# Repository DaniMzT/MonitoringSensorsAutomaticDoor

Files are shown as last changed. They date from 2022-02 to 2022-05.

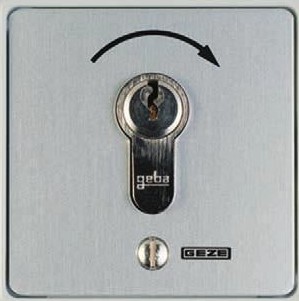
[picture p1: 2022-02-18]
Code/Website_code/htdocs/IoT/images/kb.jpg

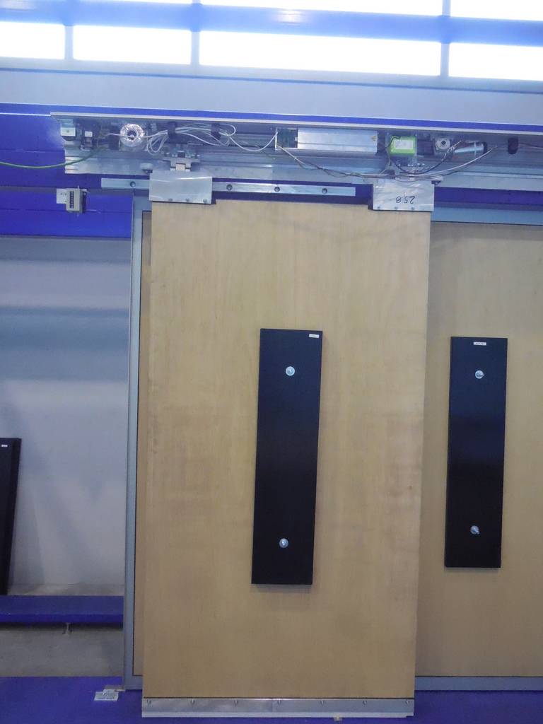
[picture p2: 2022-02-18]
Code/Website_code/htdocs/IoT/images/wooden_door-vertical.jpg

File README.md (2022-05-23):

# MonitoringSensorsAutomaticDoor
This project is a university thesis carried out in the company GEZE, focused on the automatic sliding doors tested in the laboratory. 
However, it can be extended to generic monitoring projects.
The targets of the project are:
- To acquire data from external sensors (current, temperature, humidity, position, speed and cycles)
- To save the data into a database
- To display live data and maximum/minimum values on a website, as well as providing other functionalities for the test engineers like:
  - Notification of alarms (based on the limits set by the engineers on the website) on the website and by email (email accounts registered on the website)
  - Download some specific data of tests from a specified date range 
  - Watch live streaming of the test benches (FOSCAM IP camera)
  - Perform remote activations on the bench (open/stop)

A NodeMCU is the main controller, acquiring the sensors data and sending the processed data via WiFi to a database (with a PHP file as a bridge).
There is an Arduino UNO for the acquisition of position, speed (both acquired with a home-made encoder: 2 micro photosensors,emitting to and receiving from a zebra band on the door) and limit switch activations (for door cycles).
The communication between NodeMCU and Arduino UNO is via SoftwareSerial --> not very reliable, it is the main issue to be fixed.
Database and website: based on Bitnami WAMP (package for Windows, Apache, MySQL and PHP)

Files in the project:
- Code: website, micros (NodeMCU and Arduino UNO) and database (MySQL)
- KiCAD files (to be added): schematic and printed boards

ISSUES TO BE FIXED:
- Communication between NodeMCU and Arduino UNO. SoftwareSerial is not reliable, I am afraid it is not due to my code. 
I will try to switch ports so that I can use SPI communication (currently, the SPI ports are used as GPIOs)
- Website security is weak. I have been self-learning web programming on the fly --> User identifications, work with JavaScript to process the forms, etc.

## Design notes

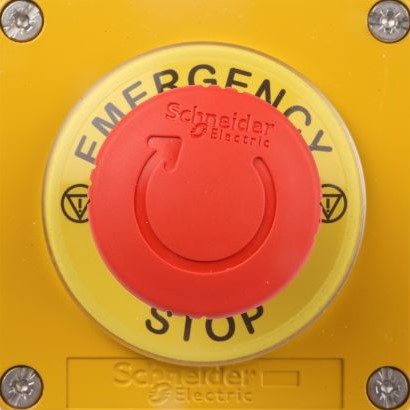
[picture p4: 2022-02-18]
Code/Website_code/htdocs/IoT/images/emStop.jpg

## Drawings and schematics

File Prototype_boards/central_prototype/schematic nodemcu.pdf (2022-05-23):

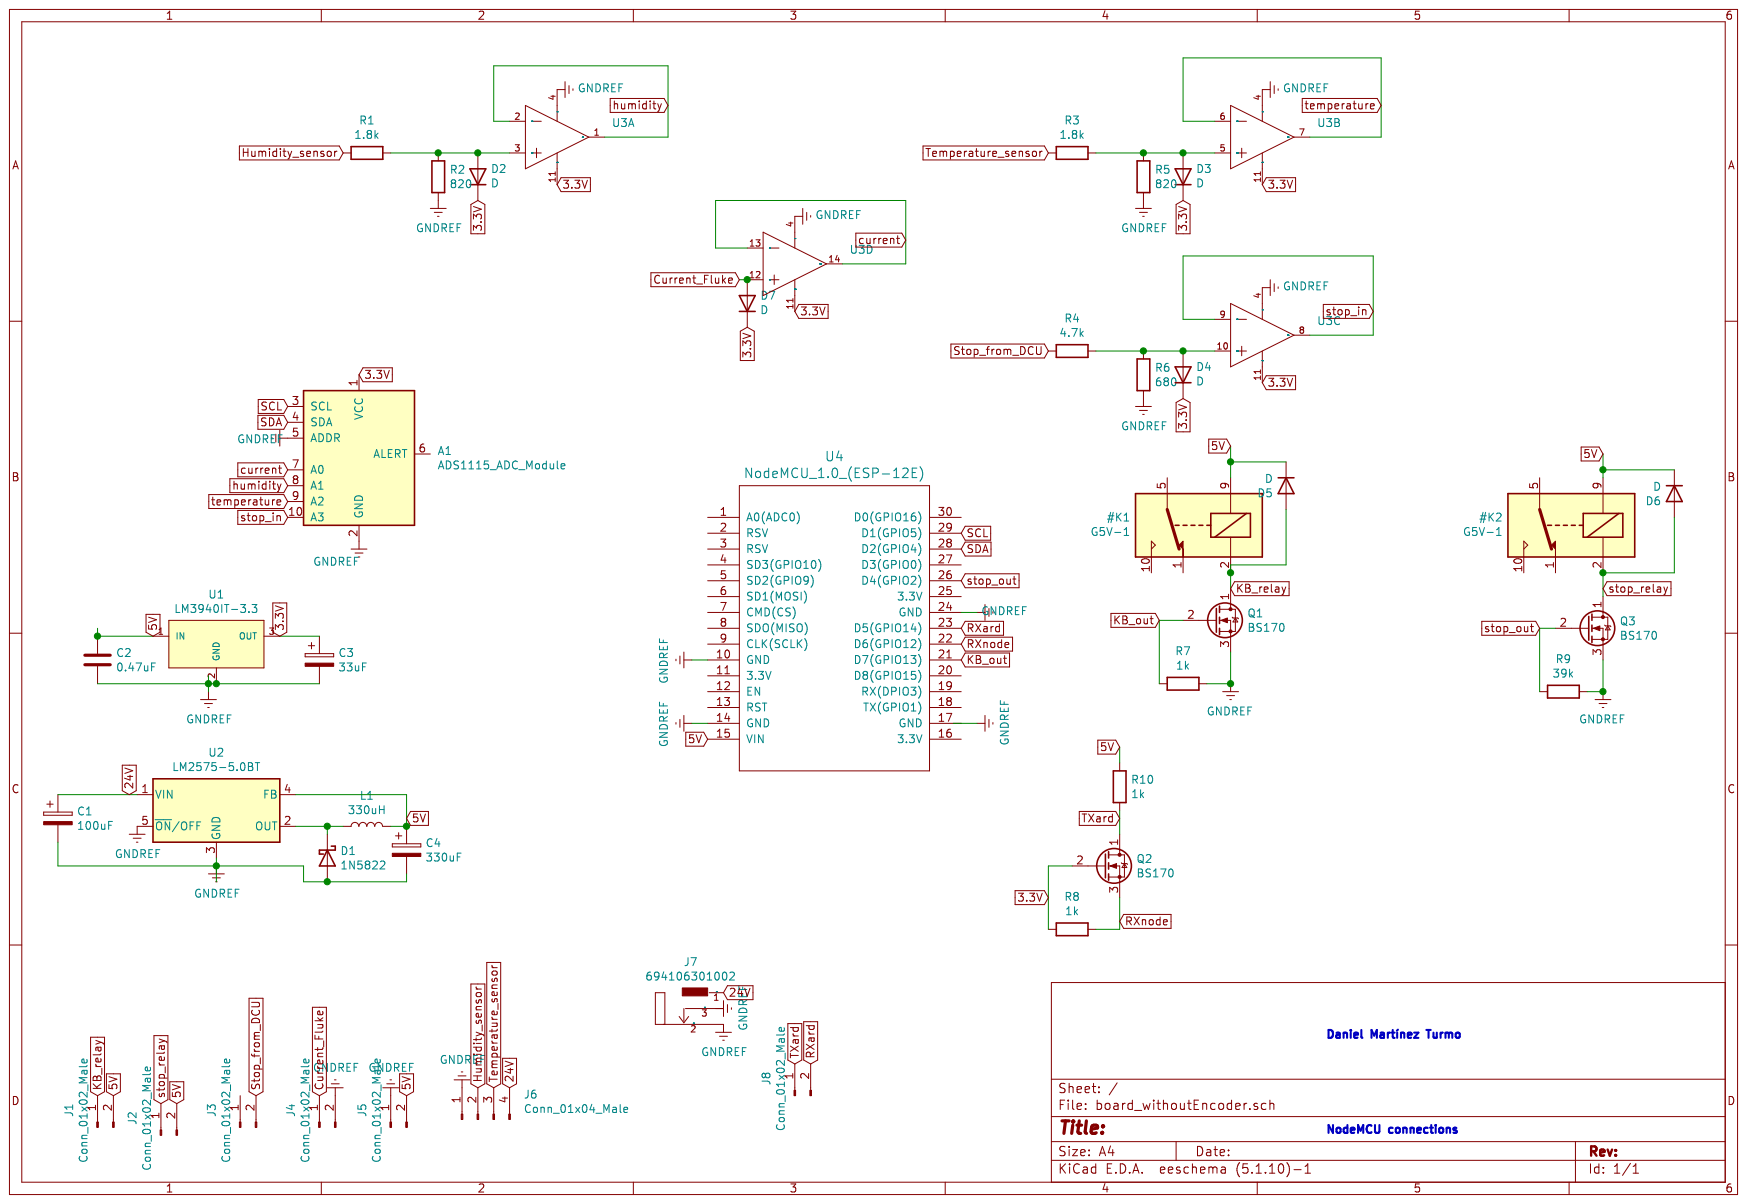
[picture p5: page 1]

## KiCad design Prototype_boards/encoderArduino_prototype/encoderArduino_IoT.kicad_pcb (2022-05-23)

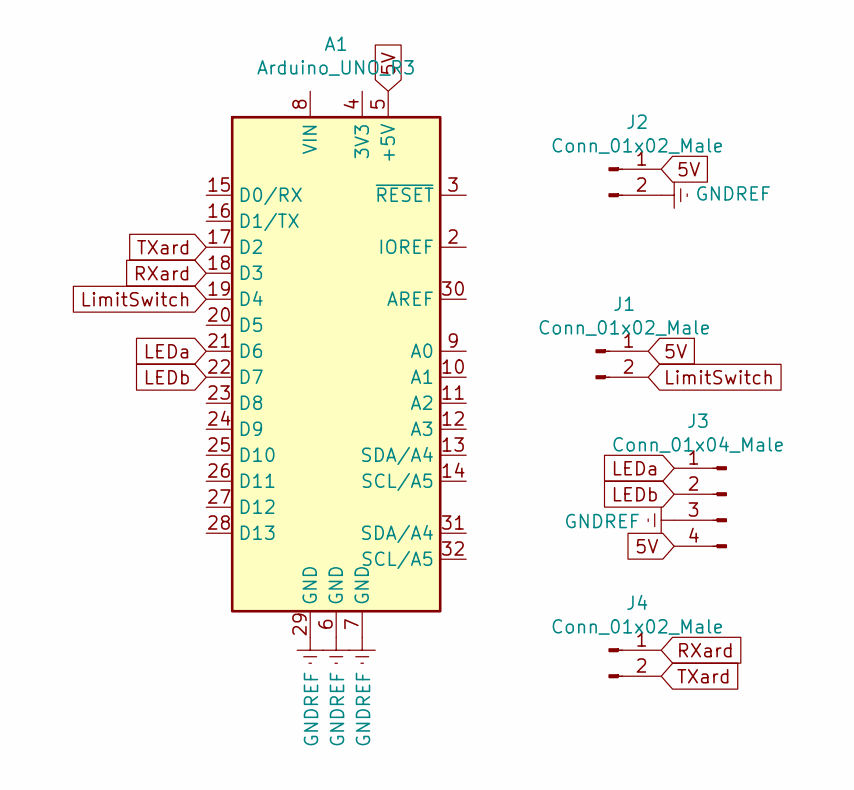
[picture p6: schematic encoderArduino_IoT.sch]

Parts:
A1: Arduino_UNO_R3; Arduino_UNO_R3_WithMountingHoles
J1, J2, J4: Conn_01x02_Male; PhoenixContact_MC_1,5_2-G-3.5_1x02_P3.50mm_Horizontal
J3: Conn_01x04_Male; PhoenixContact_MC_1,5_4-G-3.5_1x04_P3.50mm_Horizontal

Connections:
5V: A1.5 (+5V), J1.1, J2.1, J3.4
GNDREF: A1.6 (GND), A1.7 (GND), A1.29 (GND), J2.2, J3.3
LEDa: A1.21 (D6), J3.1
LEDb: A1.22 (D7), J3.2
LimitSwitch: A1.19 (D4), J1.2
RXard: A1.18 (D3), J4.1
TXard: A1.17 (D2), J4.2

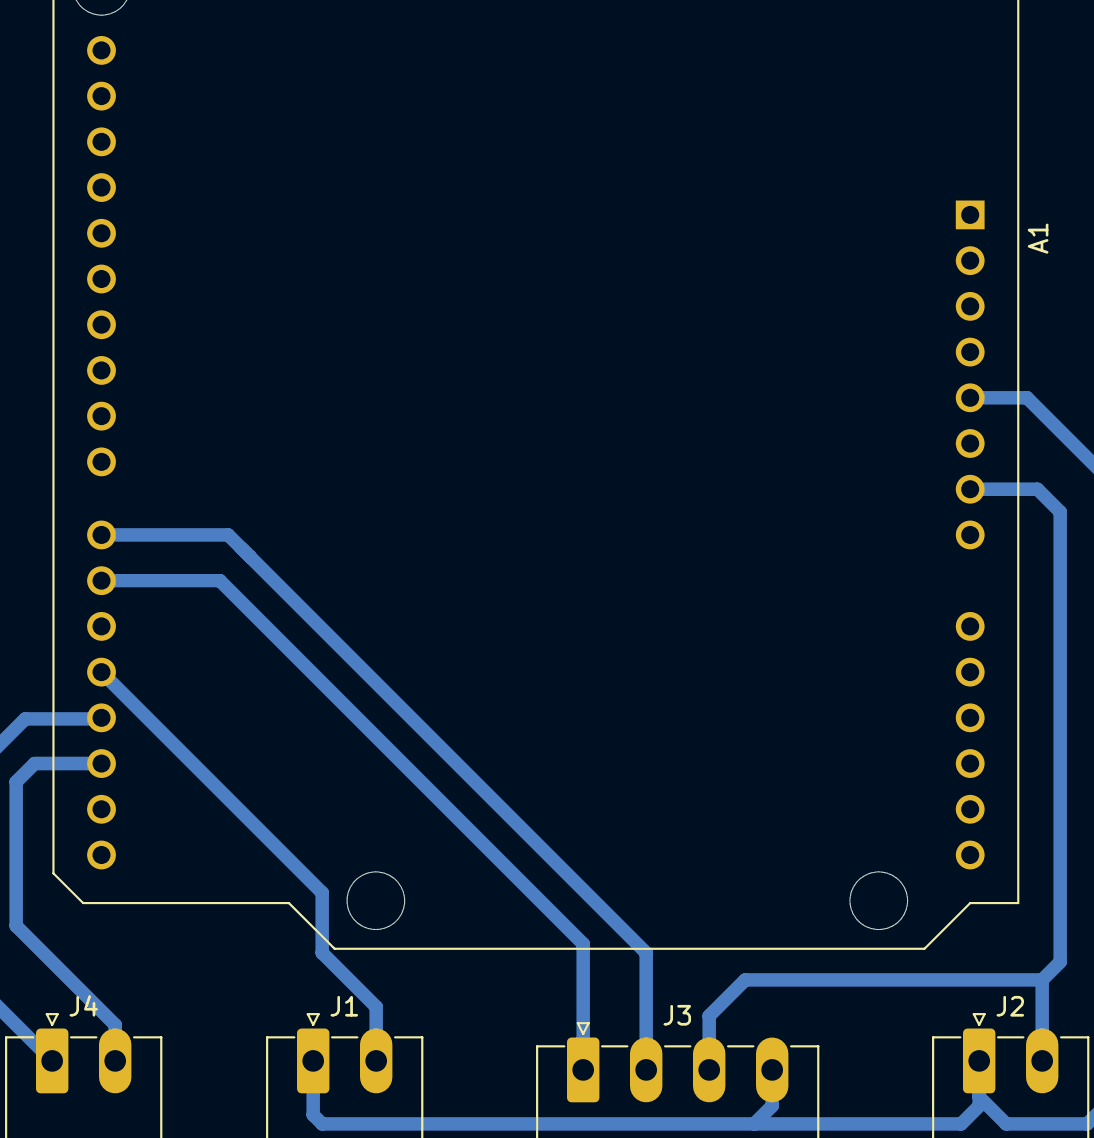
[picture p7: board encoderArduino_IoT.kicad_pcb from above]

Board: 2 copper layers, 5 parts (0 on the bottom side), 7 nets.

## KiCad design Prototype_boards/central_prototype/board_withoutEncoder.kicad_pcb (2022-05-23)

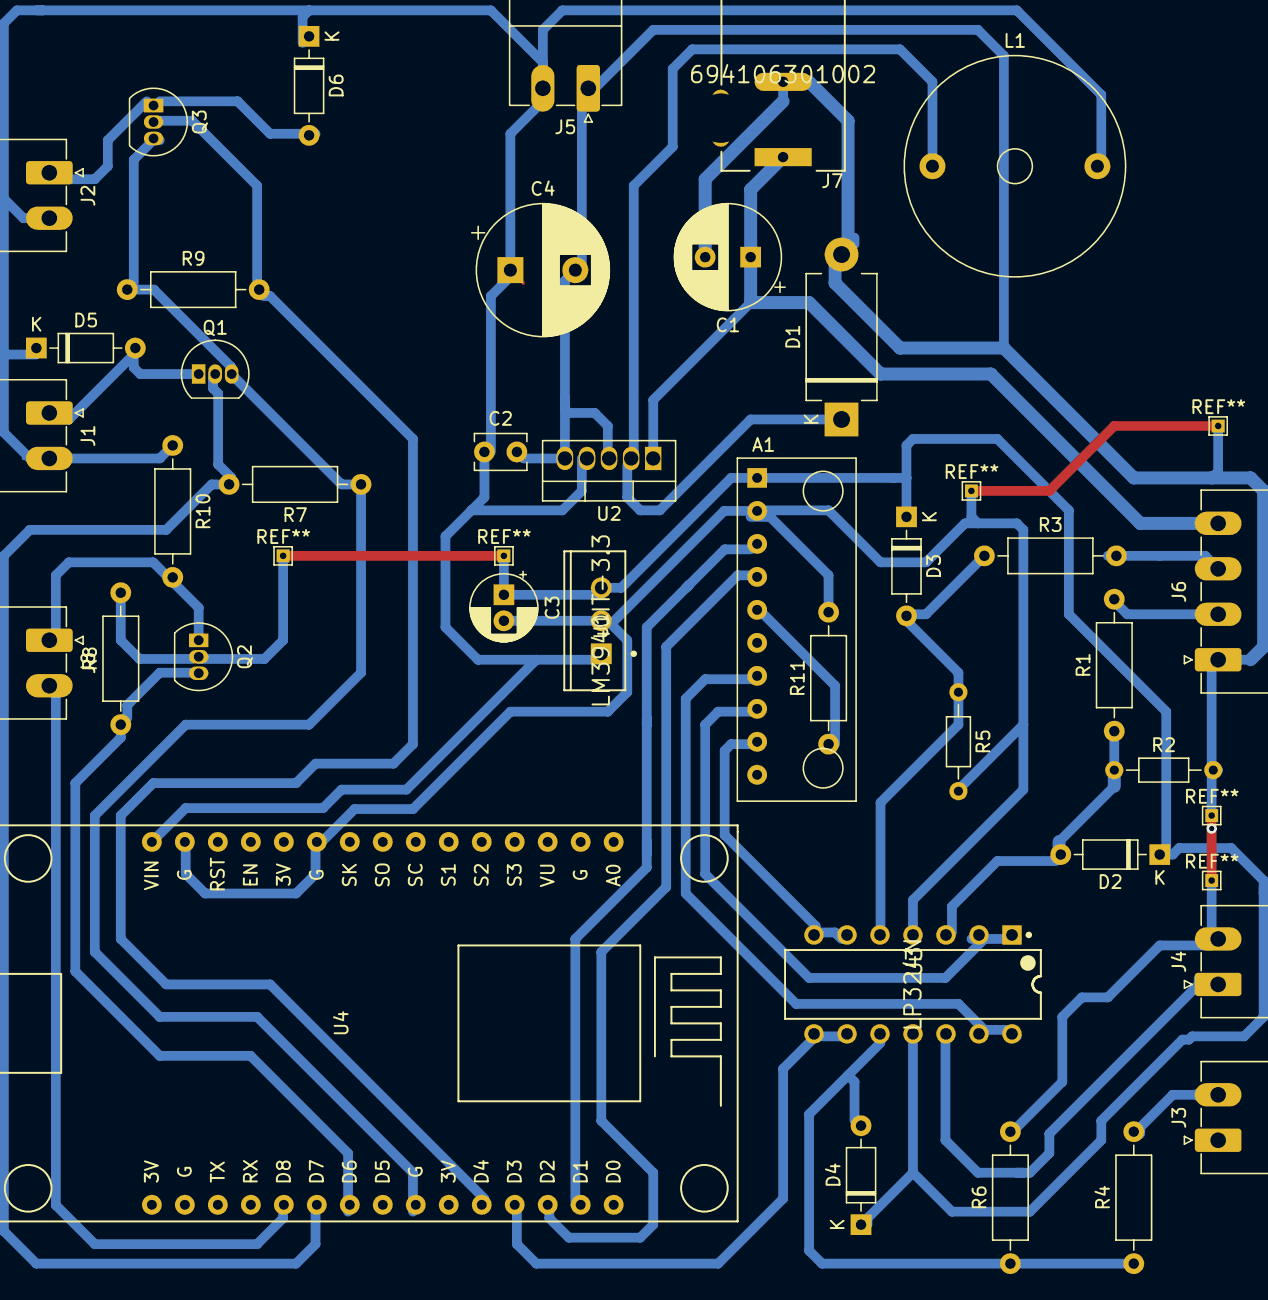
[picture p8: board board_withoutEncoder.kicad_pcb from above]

Board: 2 copper layers, 38 parts (0 on the bottom side), 26 nets.

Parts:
A1: ADS1115_ADC_Module; ADC1115_ADC_Module
C1: 100uF; CP_Radial_D8.0mm_P3.50mm
C2: 0.47uF; C_Disc_D3.8mm_W2.6mm_P2.50mm
C3: 33uF; CP_Radial_D5.0mm_P2.00mm
C4: 330uF; CP_Radial_D10.0mm_P5.00mm
D1: 1N5822; D_DO-201_P12.70mm_Horizontal
D2, D3, D4, D5, D6: D; D_DO-35_SOD27_P7.62mm_Horizontal
J1, J2, J3, J4, J5, J8: Conn_01x02_Male; PhoenixContact_MC_1,5_2-G-3.5_1x02_P3.50mm_Horizontal
J6: Conn_01x04_Male; PhoenixContact_MC_1,5_4-G-3.5_1x04_P3.50mm_Horizontal
J7: 694106301002; Wurth-694106301002-0-0-0
L1: 330uH; L_Radial_D16.8mm_P12.70mm_Vishay_IHB-1
Q1, Q2, Q3: BS170; TO-92_Inline
R1, R3: 1.8k; R_Axial_DIN0207_L6.3mm_D2.5mm_P10.16mm_Horizontal
R2, R5: 820; R_Axial_DIN0204_L3.6mm_D1.6mm_P7.62mm_Horizontal
R4: 4.7k; R_Axial_DIN0207_L6.3mm_D2.5mm_P10.16mm_Horizontal
R6: 680; R_Axial_DIN0207_L6.3mm_D2.5mm_P10.16mm_Horizontal
R7, R8, R9, R10, R11: 1k; R_Axial_DIN0207_L6.3mm_D2.5mm_P10.16mm_Horizontal
U1: LM3940IT-3.3; TI_National_Semiconductor-LM3940IT-3.3-Manufacturer_Recomme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
U2: LM2575-5.0BT; TO-220-5_Vertical
U3: LP324N; Texas_Instruments-LP324N-Manufacturer_Recommended
U4: NodeMCU_1.0_(ESP-12E); NodeMCU1.0(12-E)

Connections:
3.3V: A1.1, C3.1, D2.1, D3.1, D4.1, Q2.2, R8.2, U1.3, U3.11
5V: C2.1, C4.1, D5.1, D6.1, J1.2, J2.2, J5.2, L1.2, R10.1, U1.1, U2.4, U4.15
24V: C1.1, J6.4, J7.1, U2.1
Current_Fluke: J4.1, U3.12
GNDREF: A1.2, C1.2, C2.2, C3.2, C4.2, D1.2, J4.2, J5.1, J6.1, J7.2, Q1.3, Q3.3, R2.2, R5.2, R6.2, R7.1, R9.1, R11.2, U1.2, U2.3, U2.5, U3.4, U4.10, U4.14, U4.17, U4.24
Humidity_sensor: J6.2, R1.2
KB_out: Q1.2, R7.2, U4.21
KB_relay: D5.2, J1.1, Q1.1
unnamed: A1.5, R11.1
unnamed: D1.1, L1.1, U2.2
unnamed: D2.2, R1.1, R2.1, U3.3
unnamed: D3.2, R3.1, R5.1, U3.5
unnamed: D4.2, R4.1, R6.1, U3.10
RXard: J8.2, U4.20
RXnode: Q2.3, R8.1, U4.22
SCL: A1.3, U4.29
SDA: A1.4, U4.28
Stop_from_DCU: J3.2, R4.2
TXard: J8.1, Q2.1, R10.2
Temperature_sensor: J6.3, R3.2
current: A1.7, U3.13, U3.14
humidity: A1.8, U3.1, U3.2
stop_in: U3.8, U3.9, U4.27
stop_out: Q3.2, R9.2, U4.26
stop_relay: D6.2, J2.1, Q3.1
temperature: A1.9, U3.6, U3.7

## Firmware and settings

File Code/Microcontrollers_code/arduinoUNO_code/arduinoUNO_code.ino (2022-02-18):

#include <SoftwareSerial.h> //for software serial communication Arduino-NodeMCU
#include <StreamUtils.h>

const int pinCOUNTER = 4 ; //pin D4 GPIO4 limit switch used as a cycles counter
const int pinLEDA = 6; //pin D6 GPIO6 for LED A used for the encoder
const int pinLEDB = 7; //pin D7 GPIO7 for LED B used for the encoder

bool addCycle = true; //true if new cycle. the number of cycles is stored in database. bool size=1 byte; int size = 2 bytes (if I wanted to use 1 or 0 instead of true or false)
int lastCounter = LOW; //last state of the limit switch. HIGH/LOW from digitalRead is type int
int currentCounter = LOW; //current state of the limit switch
unsigned long time_cycle_begin = millis(); //time when cycle starts. millis() is type unsigned long
unsigned long time_cycle_previous = millis(); //time reading in the previous iteration
unsigned long time_cycle_current = millis(); //current time
float duration_cycle; //duration of the current cycle in seconds.
bool encoder_lost = false; //if encoder reading makes no sense (encoder error, either due to the sensor or to wrong reading because of too slow sampling, etc)
int LEDA; //signal LED A
int LEDB; //signal LED B
unsigned int last_Encoder_state = 4; //last encoder reading.state = 0 if{HIGH,LOW};1 if{LOW,HIGH};2 if{LOW,LOW};3 if{HIGH,HIGH};4=to access case:default first time in readEncoder
const int resolution_position = 3; //displacement in mm in every transition
int previous_position = -1; //positioning/speed will start when position==0. BETTER UNSIGNED! if the installation is correct, signed will work
int current_position = -1; //positioning/speed will start when position==0. BETTER UNSIGNED! if the installation is correct, signed will work
float current_speed = -1.0;
bool initialized = false;

//pins SW serial
const int RXard = 2; //GPIO2
const int TXard = 3; //GPIO3
SoftwareSerial swSerial(2,3); //communication SW serial Arduino-NodeMCU

//int iteration = 0;
bool ack_Node = false;
const byte limit_wait = 10; //limit to wait for the permission from Node. As short as possible to keep encoder running
unsigned int time_ArdNode = 0;

const int loop_wait = 1; //ms of wait between loop iterations
char rubbish;

void setup() {
  Serial.begin(115200); //serial port (real port)
  // Using the lowest possible data rate to reduce error ratio
  swSerial.begin(4800);//4800. 9600 was proved to work
  pinMode(pinLEDA,INPUT); //configuration digital input
  pinMode(pinLEDB,INPUT); //configuration digital input
  pinMode(pinCOUNTER,INPUT); //configuration digital input
  delay(5000);
  while (swSerial.available()!=0) {
    //setup.swSerial != 0
    rubbish = swSerial.read();
  }
  //setup.swSerial empty
  swSerial.print('N');
  
}

void loop() {
  readCounter(pinCOUNTER); //check if there is a new cycle by reading limit switch
  readEncoder(pinLEDA, pinLEDB); //position and speed calculated after reading from encoder
  ack_Node = false;
  time_ArdNode = millis();
  //send as long as Node allows ('y' received)
  while ((swSerial.available()>0)&&(ack_Node == false)&&((millis()-time_ArdNode)<limit_wait)){
    if (swSerial.read()=='S'){
      ack_Node = true;
    }
  }
  if (ack_Node == true) {
    swSerial.print('Y');//yes
    swSerial.print('<'); //start marker: <
    swSerial.print(current_position);
    swSerial.print(';');
    swSerial.print(current_speed);
    swSerial.print(';');
    swSerial.print(duration_cycle);
    swSerial.print(';');
    swSerial.print(addCycle);
    swSerial.print(';');
    swSerial.print(encoder_lost);
    swSerial.print('>');//end marker: >
  }
  
  delay(loop_wait);
}

void readCounter(int pin) {
  currentCounter = digitalRead(pin);
  addCycle = false;
  if ((currentCounter == HIGH) && (lastCounter == LOW)) { //rising edge
    initialized = true;
    //current_position = 0;
    /*Not desired to do current_position=0. If limit switch active, current pos GIVEN BY ENCODER CALCULATION should be 0.otherwise, encoder may be faulty, but we want to know encoder
      is faulty by comparing curr pos and limit switch.As well,maybe position is close to 0 but not 0 when limit switch active.If we wanted to do current_position=0,anyway we should
      modify readEncoder because currently current_position=previous_position(w/o +-resolution)*/
    addCycle = true;
    time_cycle_begin = millis();
    duration_cycle = 0;
  }
  lastCounter = currentCounter;
}

void readEncoder(int pinA, int pinB) {
  if (initialized == true) { //initialized once we know the zero position.From then, we can know absolute position.
    //switch-case only can work with integers or enumerations.
    //if statements working element by element, not array_variable == {value1,value2...} but array_variable[0]==value1 && array_variable[1]==value2 ...
    //only read encoder if last reading was not defective or,if defective,restart after every new cycle
    if ((encoder_lost == false) || ((encoder_lost == true) && (addCycle == true))) {
      encoder_lost = false; //clear encoder error
      LEDA = digitalRead(pinA);
      LEDB = digitalRead(pinB);
      time_cycle_current = millis();
      //machine of encoder states according to LED A and LED B signals
      if ((LEDA == HIGH) && (LEDB == LOW)) { //state 0
        switch (last_Encoder_state) {
          case 0:
            current_position = previous_position;
            break;
          case 2:
            current_position = previous_position + resolution_position;
            break;
          case 3:
            current_position = previous_position - resolution_position;
            break;
          case 1: //encoder lost
            encoder_lost = true;
          default:
            current_position = previous_position;
            break;
        }
        last_Encoder_state = 0;
      }
      else if ((LEDA == LOW) && (LEDB == HIGH)) { //state 1
        switch (last_Encoder_state) {
          case 1:
            current_position = previous_position;
            break;
          case 3:
            current_position = previous_position + resolution_position;
            break;
          case 2:
            current_position = previous_position - resolution_position;
            break;
          case 0: //encoder lost
            encoder_lost = true;
          default:
            current_position = previous_position;
            break;
        }
        last_Encoder_state = 1;
      }
      else if ((LEDA == LOW) && (LEDB == LOW)) { //state 2
        switch (last_Encoder_state) {
          case 2:
            current_position = previous_position;
            break;
          case 1:
            current_position = previous_position + resolution_position;
            break;
          case 0:
            current_position = previous_position - resolution_position;
            break;
          case 3: //encoder lost
            encoder_lost = true;
          default:
            current_position = previous_position;
            break;
        }
        last_Encoder_state = 2;
      }
      else if ((LEDA == HIGH) && (LEDB == HIGH)) { //state 3
        switch (last_Encoder_state) {
          case 3:
            current_position = previous_position;
            break;
          case 0:
            current_position = previous_position + resolution_position;
            break;
          case 1:
            current_position = previous_position - resolution_position;
            break;
          case 2: //encoder lost
            encoder_lost = true;
          default:
            current_position = previous_position;
            break;
        }
        last_Encoder_state = 3;
      }
      duration_cycle = (time_cycle_current - time_cycle_begin ) / 1000.0; // converted into seconds, as millis() are given in ms
      current_speed = (float(current_position) - float(previous_position)) * 1000.0 / (float(time_cycle_current - time_cycle_previous)); //substraction unsigned int returns an unsigned int
      time_cycle_previous = time_cycle_current;
      previous_position = current_position;
    }
  }
  else {
    time_cycle_previous = millis(); //for the first time in readEncoder
  }
}

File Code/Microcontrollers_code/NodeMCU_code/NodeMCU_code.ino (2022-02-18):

//in case of using Platformio or other which are not Arduino IDE --> #include <Arduino.h>
//for ESP8266
#include <ESP8266WiFi.h>
#include <ESP8266HTTPClient.h> //for the HTTP requests like GET or POST, with ESP8266 being client
#include <ESP8266WebServer.h> //for dealing with ESP8266 as a server

#include <SoftwareSerial.h> //for software serial communication Arduino-NodeMCU. CANNOT TRANSMIT AND RECEIVE SIMULTANEOUSLY

//Libraries for I2C, which we use for ADC transmission
#include <Wire.h>
#include <Adafruit_ADS1X15.h>

//ADC
Adafruit_ADS1115 adc; //object of the class for the ADC.ADDR connected to GND (0x48)
bool adc_begin; 

const int loop_wait = 200; //ms of wait between loop iterations. 200 used to work

//SW SERIAL
SoftwareSerial swSerial(12,14); //communication SW serial Arduino-NodeMCU. 12(D6)=RXnode=TXard(3); 14(D5)=TXnode=RXard(2)

  
//HTTP REQUESTS
const char* ssid = "ssidName"; //WiFi network. const char* is the same as const char *ssid, a pointer to char variable 
const char* password = "ssidPass"; //WiFi password

const char* host = "http://192.168.1.49/IoT/fromArduino.php";

//Port where ESP8266 will listen
ESP8266WebServer ESPserver(5000); //default:80.use 5000 to avoid issues,as defined in port forwarding.But when clicking the button, a warning window will appear

//SENSORS. PINMODE --> GPIO number, no D1,D2...
const int pinCURRENT = 0; //pin of ADS1115 for sensor of current. Notation used in readADC_SingleEnded()
const int pinTEMP = 2; //pin of ADS1115 for temperature sensor. Notation used in readADC_SingleEnded()
const int pinHUM = 1; //pin of ADS1115 for humidity sensor. Notation used in readADC_SingleEnded()
const int pinSTOP_out = 2; //pin D4 GPIO2 for STOP relay managed from web
const int pinKB = 13; //pin D7 GPIO13 for KB, managed from web
const int pinSTOP = 3; //pin of ADS1115 for emergency stop button activated in the test site

const float adc_res = 0.125;
const float sensitivity_Current = adc_res*300/33;//Fluke i30 sensitivity current/ADC resolution = (30000mA/3000mV)*(3000mV/3300mV)*0.125mV/bitADC
const int offset_Current = 0;//offset current given in mA
const int offset_OAc = 0; //offset current due to operational amplifier, given in bits
float current = 0; //mA
const float sensitivity_Temp = adc_res*5/313; //sensitivity temp/ADC resolution = ((50-(0))/10000mV)*(10000mV/3130mV)*0.125mV/bitADC
const int offset_Temp = 0; //offset temperature due to sensor
const int offset_OAt = 0; //-3600.offset temperature due to operational amplifier, given in bits
float temperature = 0;
const float sensitivity_Hum = adc_res*9/313; //sensitivity hum/ADC resolution = (90/10000mV)*(10000mV/3300mV)*0.125mV/bitADC
const int offset_Hum = 5; //offset humidity due to sensor
const int offset_OAh = 0; //-3456 offset humidity due to operational amplifier, given in bits
unsigned int humidity = 0;
int EmergencyStop_active = LOW; //signal from Emergency Stop button
//raw values ADC
int16_t rawT = 0; 
int16_t rawH = 0;
int16_t rawC = 0;
int16_t rawE = 0;
const float sensitivity_Em = adc_res/1000;

bool addCycle = false; //true if new cycle. the number of cycles is stored in database. bool size=1 byte; int size = 2 bytes (if I wanted to use 1 or 0 instead of true or false)
float duration_cycle = 0.0; //duration of the current cycle in seconds.
bool encoder_lost = false; //if encoder reading makes no sense (encoder error, either due to the sensor or to wrong reading because of too slow sampling, etc)
int current_position = 0; //positioning/speed will start when position==0. SHOULD BE SIGNED IF THE POSITIONING SYSTEM IS CORRECT
float current_speed = 0.0;

bool outKB = false; //used in manageOutputs
bool outSTOP = false;

//used for reading SWserial
const byte maxBuffer = 64; //64 bytes max?
bool message_begun = false;
bool message_finished = false;
char currentMessage[maxBuffer]; //avoid using String in Arduino
char tempMessage[maxBuffer];
const char startMarker = '<';
const char endMarker = '>';
char currentChar;
byte posChar = 0;
char * strtok_indexPointer; // this is used by strtok() as an index
bool swserial_available = false;
const unsigned int limit_ArdNode = 1000; //limit Arduino-Node communication; better const byte = 250 (ms, byte up to 255) ?
unsigned int time_ArdNode = 0;
bool ack_Ard = false;

int arduino_iteration = 0;

/*********************************************************************************************************************************************************************************/

void setup() {
  delay(10);
  Serial.begin(115200); //serial port (real port)
  // Using the lowest possible data rate to reduce error ratio
  swSerial.begin(4800); //put the same in Arduino.9600 used to work in tests. 4800 when using JSON.
  pinMode(pinSTOP, INPUT); //configuration digital input
  pinMode(pinSTOP_out, OUTPUT); //configuration digital output
  pinMode(pinKB, OUTPUT); //configuration digital output

  adc.setGain(GAIN_ONE); //15 bits ADS1115.Critical:current.GAIN_ONE=(4.096/2^15)*sensitCurrent = 0.125mV*20A/20000mV=0.125 mA
  adc_begin = adc.begin(0x48);//start ADS1115.  //adc_begin = adc.begin()
  delay(1);

  WiFi.mode(WIFI_OFF);        //Prevents reconnection issue (taking too long to connect)
  delay(1000);
  WiFi.mode(WIFI_STA);        //This line hides the viewing of ESP as wifi hotspot

  //Serial.println();
  WiFi.begin(ssid, password);
  while (WiFi.status() != WL_CONNECTED) { //I can improve it with a time limit
    delay(500);
  }

  //define the responses from the server according to the path received
  ESPserver.on("/KBactive", activeKB); //when the ESP receives request with pressKB on the root, the server will trigger activeKB
  ESPserver.on("/KBinactive", inactiveKB);
  ESPserver.on("/STOPactive", activeSTOP);//active on LOW! because GPIO2 (D4) needs to be HIGH during boot (there is a pull-up)
  ESPserver.on("/STOPinactive", inactiveSTOP);

  //start ESP8266 as server
  ESPserver.begin();
  manageOutputs(pinSTOP_out, pinKB, false, false); //activating another emergency stop and KB from website

}
/******************************************************************************************************************************************************************************************/
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
